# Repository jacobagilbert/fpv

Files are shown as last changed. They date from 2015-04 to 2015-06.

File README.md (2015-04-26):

# Custom FPV Related Software and Hardware
This repository contains various FPV related projects. These are side projects for me, and are free for anyone to use under the MIT license. I welcome anyone who would like to help improve on these!

I will attempt to keep this readme up-to-date and provide all resources I have used.

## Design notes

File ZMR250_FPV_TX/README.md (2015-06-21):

# Custom FPV Transmitter for ZMR250: The ZTX-23

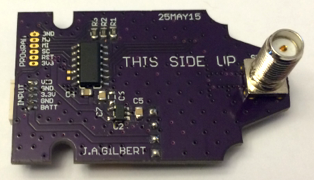
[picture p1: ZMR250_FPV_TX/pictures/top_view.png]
ZMR250 Top View


I suggest you read this entire README prior to building this, it's not that long and there are a few important considerations.

### Version 1.2 Changelog:

The version 1.2 hardware has resolved a few issues and annoyances:

- Addition of LDO to resolve SMPS noise in video
- Input connector is now a 5-pin picoblade to distinguish from the programming header
- Changed footprint for 7343 capacitors
- Switch and LED positions are changed for easier access
- Requires modification of the Pololu module

The remainder of this guide is for v1.2 only.

### Origins:

I had a number of annoyances related to the BOSCAM FPV transmitter I initially purchased for my ZRM250 quadcopter. It was difficult to change frequencies, mounting wasn't ideal, and most of all for whatever reason, it only put out 13.1 dBm (~20mW). I knew I was going to need another one, and I happened to stumble across a [German RC forum post](http://fpv-treff.de/viewtopic.php?f=23&t=5974) where an awesome guy developed a custom transmitter based around the TX5823 200mW 5.8GHz transmitter found in many pre-packaged FPV transmitters. While not exactly what I wanted, it was a great starting point and served as the inspiration for this project.

There are a number of differences from the original work, specifically the ATTiny software and PCB layout are completely new, but they get a ton of credit for all the great stuff in that forum .

### Project Objectives:

This project seeks to produce a 200mW FPV transmitter with the following specifications:

- Easily mounted securely on the ZMR250 frame
- Low profile and does not inhibit use of 6" propellers
- Simple to change channels (no buried DIP switches!)
- Direct 3S/4S power input
- Has frequency agility supporting all current receiver channels (including IRC's new 'RaceBand'!)

### Current System Status Overview:

**ATTiny Firmware:** The current ATTiny firmware has been tested on the hardware platform successfully! There are no known issues with the current software. I have used it many times and overall I am quite pleased. All 5 bands (40 channels total) have been implemented.

**Hardware:** The v2.1 boards are in and have been populated and tested - they function great. These were made through OSHPark and can be ordered [here](https://oshpark.com/shared_projects/h9UIDucG) - $12 for 3 copies. There are several optional components, which are detailed in a subsequent section.

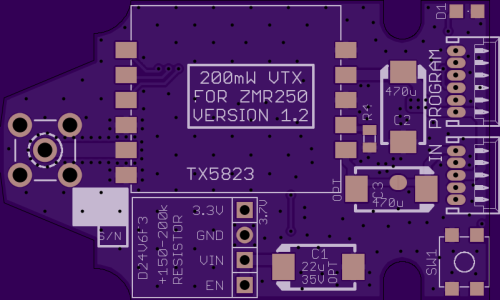
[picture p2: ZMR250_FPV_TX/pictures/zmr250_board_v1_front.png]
ZMR250 PCB Front


The RF path is a properly dimensioned CPWG transmission line, and while just at the length where it begins to matter (and it's FR4 at 5.8 GHz...), I figured it would be fun to do it properly. The trace is 55 mils wide with 9 mil spacing on 1.6 mm FR4, so the line has an impedance of between 49 and 51 ohms depending on the dielectric constant (I assume it's somewhere between 4.3 and 4.6 which should be reasonable).

**Weight:** While reducing weight was not a project objective, 250 racers and their pilots are weight-conscious if not sensitive. I made a few measurements and here is how this transmitter measures up. I was previously using a TS351 in a neat 3D printed holder, but it was pretty heavy:

| Hardware | Weight | Comments |
|---|---|---|
|BOSCAM TS351  |23.7g |Transmitter only, no mounting hardware |
|TS5823 |8g |Transmitter only, no mounting hardware |
|ZTX-23 |**13.3g** |Includes all mounting and cables! |
|SMA Extension |7g |30.7g with BOSCAM and no mounting hardware |

So this transmitter is not the lightest transmitter out there, but considering this includes all material required to securely install the transmitter to the frame, I am very pleased.

**Video Quality:** The ZTX-23 works really great. I tested bypassing the 3.3V LDO and using the Pololu module output directly, and one module looked okay, while the other had significant noise. With the LDO, crystal clear video. At this point I recommend using the LDO (it's ~$0.50) and making the modification to the Pololu module mentioned below.

### Repository Structure:

- eagle/			Eagle PCB files
- attiny/			ATTiny related files and firmware for board
- FPV_TX_BOM.xlsx		Bill of materials to populate boards
- ZMR250_FPV_TX_v1.2.zip	Compressed archive of all gerber files
- README_v1.0.md		Version 1.0 README, out of date but preserved
- README.md			This README

### Bill of Materials:

BOM is up. There are only a handful of components, but the large capacitors are all 7343 size tantalum and the small capacitors are all 0.1uf decoupling caps, the Pololu module is a 500mA 3.3V SMPS, R1 is 330 ohm and R2/R3 are 3.3k. The LDO (U2) is an AP2112 3.3V fixed-output reg. All the small passives are 0805 (however SparkFun's 0805 footprint is a little tight... If you have them, use 0603 for bypass capacitor and resistors).

### Component Modifications:

Both the TX5823 module and Pololu SMPS must be modified before they can be used for this application.

**TX5823 Module Modifications:** It is necessary to modify the TX5823 module so it is able to operate in SPI mode. The modification only require the removal of a single resistor, however it is under the metal shield on the module so you will need to remove that first. This information is available in either the datasheet of the RTC6705 chip.

The easiest way to make the modification is to work one side at a time (they are soldered on two sides) with a soldering iron and precision slotted screwdriver. Use the screwdriver between the module board and shield to *gently* apply pressure while melting the solder. If you work carefully, alternating sides, and taking breaks to allow the module to cool down it is fairly easy to remove the shield. Clean up any excess solder, and remove the resistor shown in the following image:

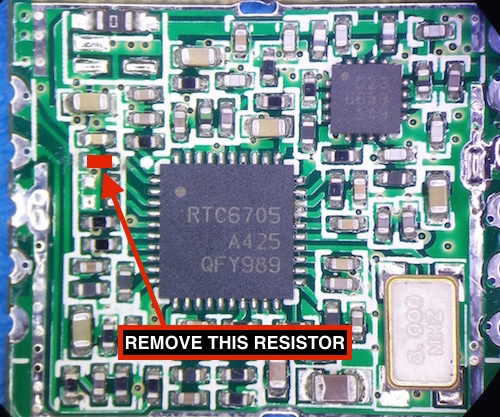
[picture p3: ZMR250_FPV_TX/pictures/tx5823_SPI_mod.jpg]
TX5823 Module RX5823 with shield removed


After removing the resistor, inspect the board (preferrably under a magnifying glass) to ensure you have not accidentally caused any shorts or displaced any other components; replace the shield. This only needs to be done once so you can re-solder the shield to the module PCB.

More information regarding SPI mode operation is available in the limited datasheet, and under the 'attiny' directory.

**Pololu Module Modification:** In order to use the 3.3V LDO, the input must be around 3.6V due to the dropout voltage. This requires a change in the Pololu module, which fortunately is simple - soldering a resistor in parallel with 22.1k R2 on the Pololu module will increase the module output voltage by approximately 350mV and will properly power the LDO. This combination has good efficency on 3S/4S and provides clean power.

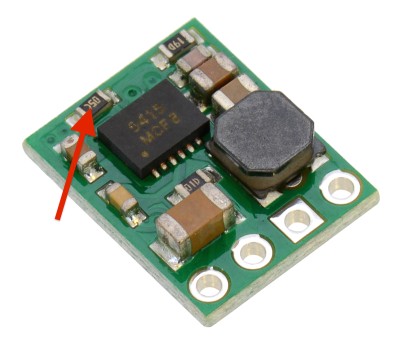
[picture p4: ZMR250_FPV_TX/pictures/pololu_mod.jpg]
Pololu SMPS Pololu Resistor Change


The resistor that must be changed by adding another in parallel is shown above, simply solder a ~150k resistor in parallel with it. This value can be deterined from the datasheet for the SMPS controller used, available from Pololu.

### Mounting Transmitter:

One of the design criteria for this transmitter was mounting natively to the ZMR250 frame. Consistant with that, it has been designed to mount cleanly to the rear of the top plate, though the hole in the rear must be drilled out with a 0.25" bit to accomodate the SMA connector. By mounting the SMA connector directly to the frame, it is very unlikely that a crash will damage the transmitter. Be careful drilling carbon fiber as it can be a little tricky, and don't inhale the dust!

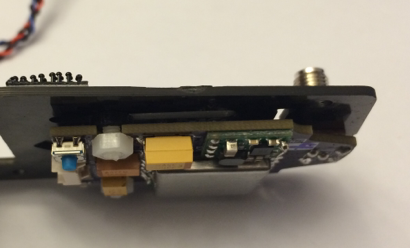
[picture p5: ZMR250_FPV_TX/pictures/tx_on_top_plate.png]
TX Mounted Transmitter on top plate


On the other end from the SMA connector are two slots that will nicely fit M3 nylon hardware. A spacer is needed to keep some standoff from the conductive frame. I used the smallest diameter HQ propeller mounting bushings since they were a pretty good fit but I'll probably 3D print some spacers that are sized better and post the files when I am happy.

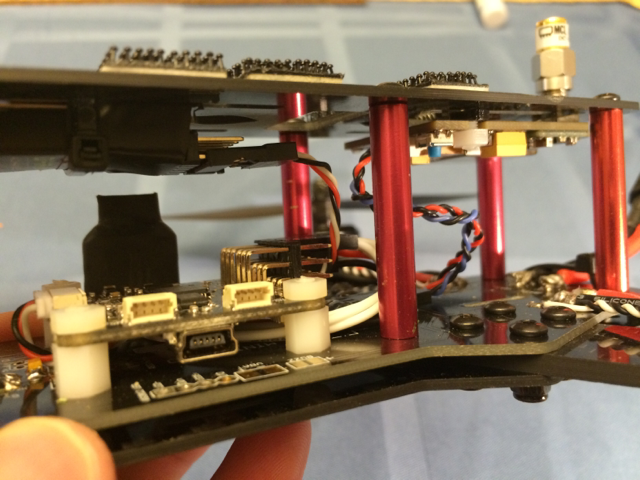
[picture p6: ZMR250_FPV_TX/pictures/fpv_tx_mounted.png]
Mounting Mounting FPV Transmitter


### Connectors:

There are two connectors on the board, a 5 pin Molex PicoBlade PTH connector for power and video input, and a 6 pin PicoBlade PTH connector for programming. I recommend populating only the 5 pin input connector so they are not confused when conecting hardware. To program the microcontroller, I bend the pins slightly on the 6 pin header so they press-fit securely and remove the connector when I am through.

### Transmitter Operation:

The transmitter will remember the last channel used and will automatically configure to this channel on startup. To view the current frequency, you can push the button once quickly and the LED will flash the current band (1-5) followed by a brief pause, followed by the current channel (1-8). To change the frequency, the following procedure should be used:

1. Press and hold the button until the LED turns off and immediately release it. In order to prevent accidental channel changing if you hold it too long, or release it too early it will not set the frequency.
2. The LED will flash quickly and stop. Press the button to set the band (eg: 3 presses will select band 3, "Band E"). If you press the button more than 5 times (the total number of supported bands), it will loop back to 1.
3. Wait for the LED to flash quickly again and set the channel using the same procedure as above. There are 8 channels in each band, and pressing more than 8 times will loop back to 1.
4. Release the button and wait for confirmation that the band has been set (flashes indicating the band, followed by the channel). The transmitter is now reconfigured and will immediately update the frequency of the module, and will start with the new channel in the future.
5. If the button is not pressed to select the band or channel, the frequency selection mode will exit and flash the LED quickly many times. There will be no change to the current or startup channel.

I think I like this scheme but I'm not sure; it might change. Either way, it's a good start that only requires one button and one LED.

### Optional Components:

**Video Input Capacitor:** The TX5823 module specifies a 470uF capacitor on the video input line (C3). These are rather expensive, and I'm not sure it is strictly necessary so I added pads that can be solder-jumpered to bypass the capacitor. I have tested both with and without this cap, and could not see a difference. I will most likely not purchase these again.

**Pololu Module Capacitor:** Pololu recommends the use of a large value capacitor to prevent damage from any turn-on voltage spike. They suggest an input of under 20V with short leads should be fine, but I included the pads anyway. I include them just in case, but like the video input cap, these are fairly expensive. If you do use one, make sure it is rated for the appropriate voltage.

**Audio Grounding Resistor:** I included pads for a resistor (R4) that can be used to terminate the audio input, which is no longer connected to the input connector. Feel free to omit this.

**Noise Reduction Capacitor:** The LDO NR capacitor (C6) should only be used with LDOs that require this. The AP2112 I have in the BOM has this pin as a NC and thus C6 should NOT be populated.

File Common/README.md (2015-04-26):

# Common files and components

Here are common components such as libraries for Eagle or Arduino, as well as datasheets for parts and other useful but not project-specific items.

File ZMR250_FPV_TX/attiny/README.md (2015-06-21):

# ATTiny Related Documents

The ATTiny84 firmware was written in Arduino because it's quick and easy, and I want the project to be approachable by non-professionals. I'll try to upload a hex file at some point though for those who are not Arduino inclined. Programming instructions are based on the [work by HighLowTech](http://highlowtech.org/?p=1695) and are pretty straightforward. A dedicated programming header is located on the board, but that might be removed in future versions since firmware should not need to change very often.

I targeted an ATTiny84 because it fit and they are still relatively inexpensive, and it let me be lazy in programming and layout, and it does not require dual-purposing pins. The sketch will compile for an ATTiny44, and shouldn't be too hard to get into an ATTiny24. Currently the Arduino IDE reports the program size as 2,156 bytes (26% of the ATTiny84).

### Files:

- attiny84_transmitter.ino	Arduino 1.6 sketch for ATTiny84
- attiny_arduino_1.6.zip	ATTiny support for Arduino 1.6
- TX_Channel_Calculator.xlsx	Excel spreadsheet for calculating register values

### Programming the ATTiny

It is important to note that the ATTiny runs from the same 3.3V supply as the video transmitter, and the VTX will be powered anytime the ATTiny is! Be sure to connect an antenna, or terminate the SMA connector so the RFIC output stage is not damaged by reflected power. The board has a dedicated programming port and current-limiting resistors on MOSI and SCK lines to allow for programming from a 5V arduino device. I don't have a dedicated Atmel programmer, so this is what I do.

This is what I do to program: connect RST, MOSI, MISO, SCK, and GND from connector X3 to pins 10-13 + GND on an Arduino board with the Arduino ISP sketch loaded. Terminate the antenna port and then apply power to VBATT on connector X2. Then hit the upload button on the Arduino IDE. The first time you program the chip, before you program, you need to make sure "internal 8MHz" is selected for clock source and burn the bootloader. The link above covers this in much better detail.

### Register Settings

The RTC6705 RFIC has two 20-bit registers that control the frequency synthesizer, 0x00 and 0x01. The 0x00 (Synthesizer Register A) register contains the R-counter divider in the low 15 bits. The 0x01 register contains the N-counter divider in the upper 13 bits and the A-counter divider in the lower 7 bits.

The default R-counter divider value (0x190 = 400d) provides for 40kHz tuning resolution, which is more than sufficient, so it is not changed. The values for the 0x01 register for each channel are pre-calculated and stored in PROGMEM. These values were derived from the equations in the TX_Channel_Calculator spreadsheet.

At initial turn-on, the registers are set to the last stored frequency which is written to onboard EEPROM after every successful channel change. This initial frequency setting procedure is performed several times at startup after varying delay. This is to reduce the amount of interference the default settings might cause to other FPV fliers in the area. 100ms delay proved too short to reliably tune the TX chip, so we attempt to tune it to the last known frequency after 100ms, 300ms, and 500ms - if it's stupid and it works it's not stupid :).

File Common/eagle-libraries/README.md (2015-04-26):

# Common Libraries
This directory contains libraries used by the various projects, both those developed by me, and archived versions of commercial/other libraries that I have incorporated.

## BOSCAM_5G8.lbr
Eagle library contianing BOSCAM 5.8GHz modules:

1. TX5823 200mW FM Transmitter (pin compatible with 10mW TX5813)

2. RX5808 FM Receiver (identical to RX5880)

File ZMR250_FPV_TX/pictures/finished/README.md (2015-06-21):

### IMAGE PREVIEW:

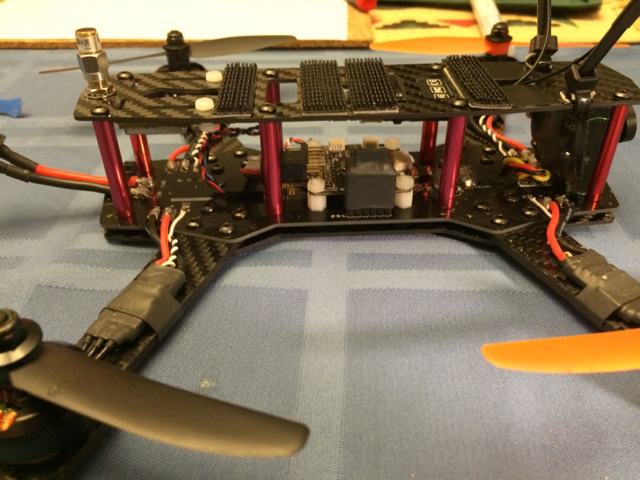
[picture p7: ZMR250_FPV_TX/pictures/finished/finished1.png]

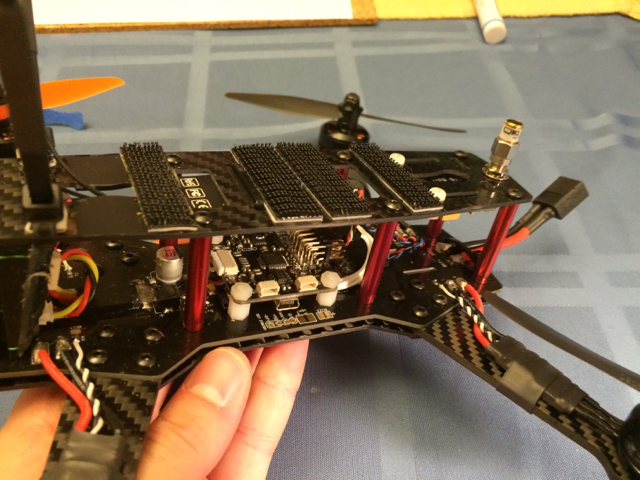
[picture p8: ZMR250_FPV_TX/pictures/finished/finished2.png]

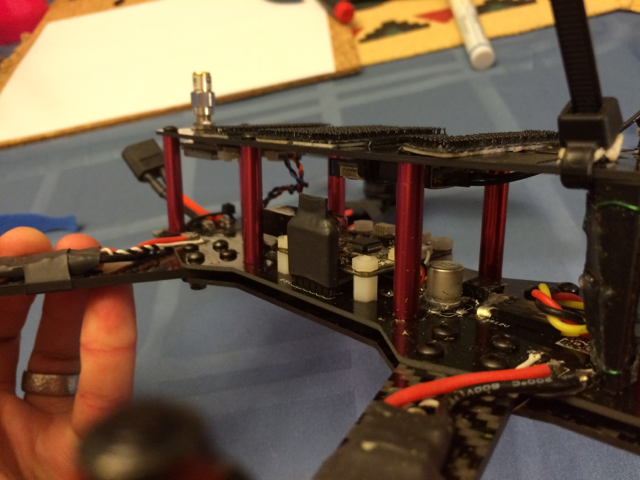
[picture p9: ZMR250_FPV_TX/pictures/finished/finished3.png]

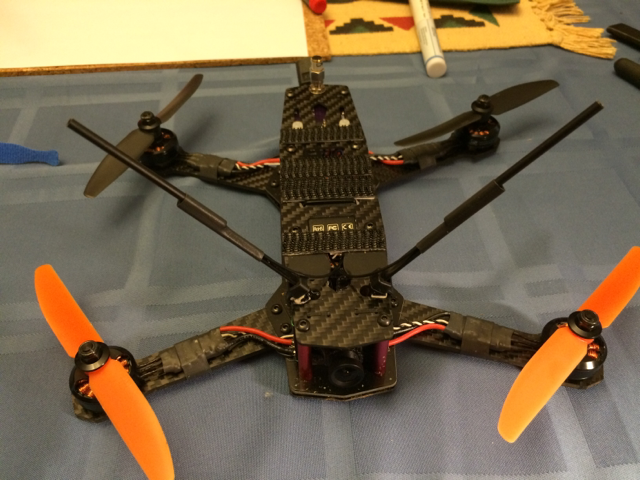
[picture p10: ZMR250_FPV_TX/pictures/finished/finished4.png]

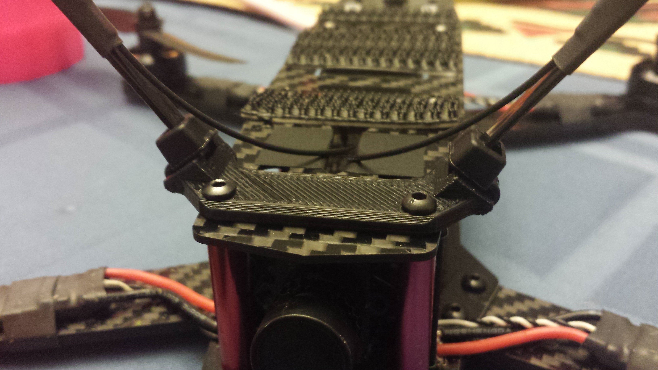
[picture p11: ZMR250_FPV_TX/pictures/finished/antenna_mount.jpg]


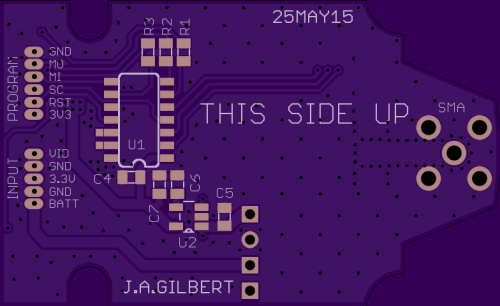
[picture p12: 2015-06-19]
ZMR250_FPV_TX/pictures/zmr250_board_v1_back.png

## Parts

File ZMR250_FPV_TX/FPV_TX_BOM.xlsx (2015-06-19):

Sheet: BOM-TXv1.0
 |  |  |  | Quantity
Name | Specs | Digikey Part Number | Digikey Link | Per board | Suggested
Connector | 6 pin male | WM1746-ND | http://www.digikey.com/product-detail/en/0530480610/WM1746-ND/242868 | 2 | 2
Connector | 6 Pin female | WM1724-ND | http://www.digikey.com/product-detail/en/0510210600/WM1724-ND/242846 | 2 | 2
Connector | Female Pins | WM1142CT-ND | http://www.digikey.com/product-detail/en/0500798000/WM1142CT-ND/467835 | 12 | 25
SMA | Tall | CONSMA008-ND | http://www.digikey.com/product-detail/en/CONSMA008/CONSMA008-ND/1577219 | 1 | 1
uC | ATTiny | ATTINY84A-SSU-ND | http://www.digikey.com/product-detail/en/ATTINY84A-SSU/ATTINY84A-SSU-ND/3046522 | 1 | 1
Resistor | 0805 / 3.3k | RHM3.30KCHCT-ND | http://www.digikey.com/product-detail/en/MCR10ERTF3301/RHM3.30KCHCT-ND/2796529 | 3 | 10
Resistor | 0805 / 1k | RHM1.00KCHCT-ND | http://www.digikey.com/product-detail/en/MCR10ERTF1001/RHM1.00KCHCT-ND/2796512 | 3 | 10
Resistor | 0805 / 330 | RHM330CHCT-ND | http://www.digikey.com/product-detail/en/MCR10ERTF3300/RHM330CHCT-ND/2796528 | 1 | 1
LED | Green (2.1V) | 160-1423-1-ND | http://www.digikey.com/product-detail/en/LTST-C171GKT/160-1423-1-ND/386792 | 1 | 1
Module Cap | 470uF | 478-4146-1-ND | http://www.digikey.com/product-detail/en/TPSE477K006R0050/478-4146-1-ND/1164482 | 1 | 1
Switch | SPST | 7914G-000ECT-ND | http://www.digikey.com/product-detail/en/7914G-1-000E/7914G-000ECT-ND/158366 | 1 | 1
Capacitor | Decoupling | 399-1284-1-ND | http://www.digikey.com/product-detail/en/C0805C105K4RACTU/399-1284-1-ND/416060 | 1 | 10
Pololu Cap | 35V/33u | 399-8536-1-ND | http://www.digikey.com/product-detail/en/T495X336K035ATE250/399-8536-1-ND/3472259 | 1 | 1
Video Cap | Video | 478-9450-1-ND | http://www.digikey.com/product-detail/en/TCJD477M002R0050/478-9450-1-ND/5001662 | 1 | 1
Not Digikey Stuff
Plolou SMPS | 3.3V / 500mA | D24V5F3 | https://www.pololu.com/product/2842 | 1 | 1
TX Module |  |  | http://www.foxtechfpv.com/tx5823-200mw-8ch-58g-tx-module-for-nano-flyers-p-272.html | 1 | 1
Boards |  |  | OSHPark | 1 | 1

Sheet: BOM-TXv1.2
 |  |  |  | Quantity
Name | Specs | Digikey Part Number | Digikey Link | Per board | Suggested | Comments
Connector | 5 pin male | WM1745-ND | http://www.digikey.com/product-detail/en/0530480510/WM1745-ND/242867 | 1 | 1
Connector | 5 Pin female | WM1723-ND | http://www.digikey.com/product-detail/en/0510210500/WM1723-ND/242845 | 1 | 1
Connector | 6 pin male | WM1746-ND | http://www.digikey.com/product-detail/en/0530480610/WM1746-ND/242868 | 1 | 1
Connector | 6 Pin female | WM1724-ND | http://www.digikey.com/product-detail/en/0510210600/WM1724-ND/242846 | 1 | 1
Connector | Female Pins | WM1142CT-ND | http://www.digikey.com/product-detail/en/0500798000/WM1142CT-ND/467835 | 11 | 25
SMA | Tall | CONSMA008-ND | http://www.digikey.com/product-detail/en/CONSMA008/CONSMA008-ND/1577219 | 1 | 1
uC | ATTiny | ATTINY84A-SSU-ND | http://www.digikey.com/product-detail/en/ATTINY84A-SSU/ATTINY84A-SSU-ND/3046522 | 1 | 1
LDO | 3.3V / 600mA | AP2112K-3.3TRG1DICT-ND | http://www.digikey.com/product-detail/en/AP2112K-3.3TRG1/AP2112K-3.3TRG1DICT-ND/4505257 | 1 | 1
Resistor | 0805 / 150k | RHM150kCHCT-ND | http://www.digikey.com/product-detail/en/MCR10ERTF1503/RHM150KCHCT-ND/4084575 | 1 | 1 | For SMPS
Resistor | 0805 / 3.3k | RHM3.30KCHCT-ND | http://www.digikey.com/product-detail/en/MCR10ERTF3301/RHM3.30KCHCT-ND/2796529 | 4 | 10
Resistor | 0805 / 330 | RHM330CHCT-ND | http://www.digikey.com/product-detail/en/MCR10ERTF3300/RHM330CHCT-ND/2796528 | 1 | 1
LED | Green (2.1V) | 160-1423-1-ND | http://www.digikey.com/product-detail/en/LTST-C171GKT/160-1423-1-ND/386792 | 1 | 1
Switch | SPST | 7914G-000ECT-ND | http://www.digikey.com/product-detail/en/7914G-1-000E/7914G-000ECT-ND/158366 | 1 | 1
Module Cap | 470uF | 478-4146-1-ND | http://www.digikey.com/product-detail/en/TPSE477K006R0050/478-4146-1-ND/1164482 | 1 | 1
Capacitor | Decoupling | 399-1284-1-ND | http://www.digikey.com/product-detail/en/C0805C105K4RACTU/399-1284-1-ND/416060 | 4 | 10
Pololu Cap | 35V/33u | 399-8536-1-ND | http://www.digikey.com/product-detail/en/T495X336K035ATE250/399-8536-1-ND/3472259 | 1 | 1 | OPTIONAL?
Video Cap | Video | 478-9450-1-ND | http://www.digikey.com/product-detail/en/TCJD477M002R0050/478-9450-1-ND/5001662 | 1 | 1 | OPTIONAL?
Not Digikey Stuff
Plolou SMPS | 3.3V / 500mA | D24V5F3 | https://www.pololu.com/product/2842 | 1 | 1
TX Module | 200mW 5.8G | TX5823 | http://www.foxtechfpv.com/tx5823-200mw-8ch-58g-tx-module-for-nano-flyers-p-272.html | 1 | 1
PCB |  |  | OSHPark | 1 | 1
Wire | 28/30 AWG |  | Recommend 30AWG silicon wire - for connector cables

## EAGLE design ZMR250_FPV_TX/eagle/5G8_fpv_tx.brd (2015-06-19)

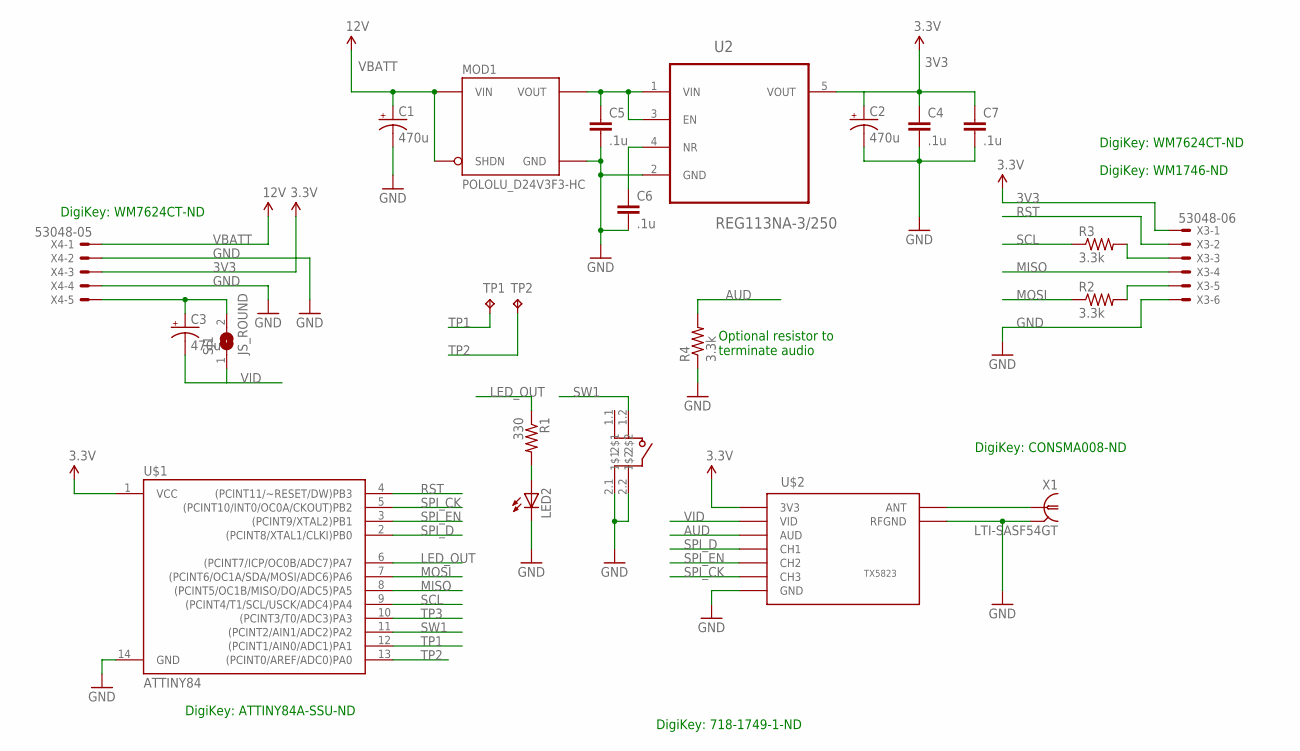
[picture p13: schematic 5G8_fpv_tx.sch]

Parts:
C1, C2, C3: 470u; VISHAY_D
C4, C5, C6, C7: .1u; 0805
LED2: LEDCHIPLED_0805; CHIPLED_0805
MOD1: POLOLU_D24V3F3-HC; POLOLU_D24V3F_HC
R1: 330; 0805
R2, R3, R4: 3.3k; 0805
SJ1: JS_ROUND; SJ_ROUND
TP1, TP2: TPTP06SQ; TP06SQ
U2: REG113NA-3/250; SOT95P280X145-5N
U$1: ATTINY84; SO14
U$2: TX5823
U$3: BOURNS_7814G_SW; 7914G
X1: LTI-SASF54GT
X3: 53048-06
X4: 53048-05

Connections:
3V3: C2.+, C4.1, C7.1, U2.5 (VOUT), U$1.1 (VCC), U$2.P$4 (3V3), X3.1, X4.3
ANT: U$2.P$10 (ANT), X1.1
AUD: R4.2, U$2.P$2 (AUD)
GND: C1.-, C2.-, C4.2, C5.2, C6.2, C7.2, LED2.C, MOD1.G (GND), R4.1, U2.2 (GND), U$1.14 (GND), U$2.P$3 (GND), U$2.P$5 (GND), U$2.P$9 (RFGND), U$2.P$11 (RFGND), U$3.2.1 (2$1), U$3.2.2 (2$2), X1.2, X1.3 (2), X1.4 (2), X1.5 (2), X3.6, X4.2, X4.4
LED: LED2.A, R1.2
LED_OUT: R1.1, U$1.6 ((PCINT7/ICP/OC0B/ADC7)PA7)
MISO: U$1.8 ((PCINT5/OC1B/MISO/DO/ADC5)PA5), X3.4
MOSI: R2.1, U$1.7 ((PCINT6/OC1A/SDA/MOSI/ADC6)PA6)
MOSI_: R2.2, X3.5
unnamed: C5.1, MOD1.O (VOUT), U2.1 (VIN), U2.3 (EN)
unnamed: C6.1, U2.4 (NR)
RST: U$1.4 ((PCINT11/~RESET/DW)PB3), X3.2
SCL: R3.1, U$1.9 ((PCINT4/T1/SCL/USCK/ADC4)PA4)
SCL_: R3.2, X3.3
SPI_CK: U$1.5 ((PCINT10/INT0/OC0A/CKOUT)PB2), U$2.P$8 (CH3)
SPI_D: U$1.2 ((PCINT8/XTAL1/CLKI)PB0), U$2.P$6 (CH1)
SPI_EN: U$1.3 ((PCINT9/XTAL2)PB1), U$2.P$7 (CH2)
SW1: U$1.11 ((PCINT2/AIN1/ADC2)PA2), U$3.1.2 (1$2)
TP1: TP1.TP, U$1.12 ((PCINT1/AIN0/ADC1)PA1)
TP2: TP2.TP, U$1.13 ((PCINT0/AREF/ADC0)PA0)
TP3: U$1.10 ((PCINT3/T0/ADC3)PA3)
VBATT: C1.+, MOD1.I (VIN), MOD1.S (SHDN), X4.1
VID: C3.-, SJ1.1, U$2.P$1 (VID)
VID_IN: C3.+, SJ1.2, X4.5

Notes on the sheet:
DigiKey: WM7624CT-ND
DigiKey: ATTINY84A-SSU-ND
DigiKey: CONSMA008-ND
DigiKey: 718-1749-1-ND
DigiKey: WM1746-ND
Optional resistor to terminate audio

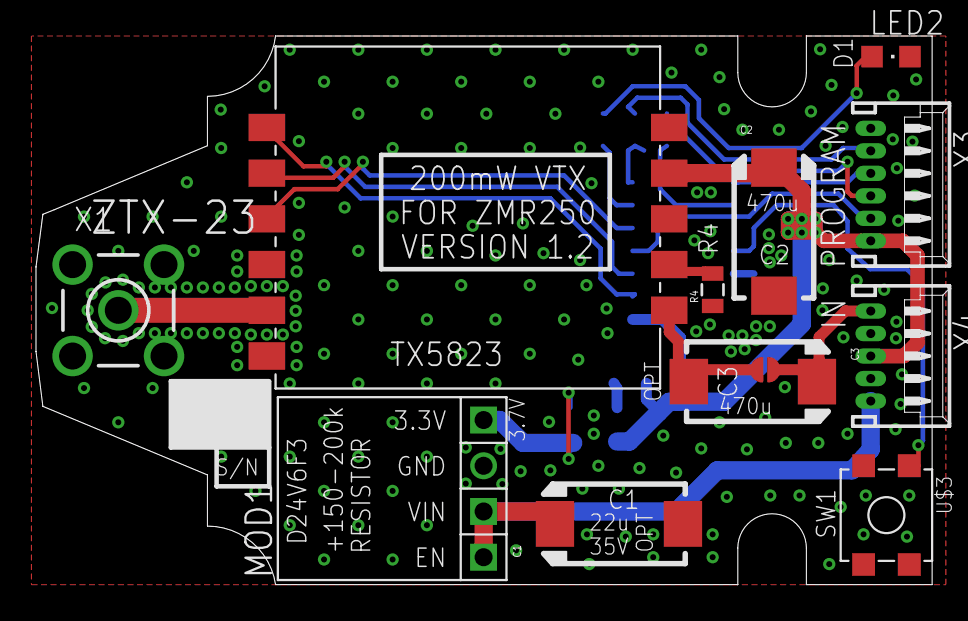
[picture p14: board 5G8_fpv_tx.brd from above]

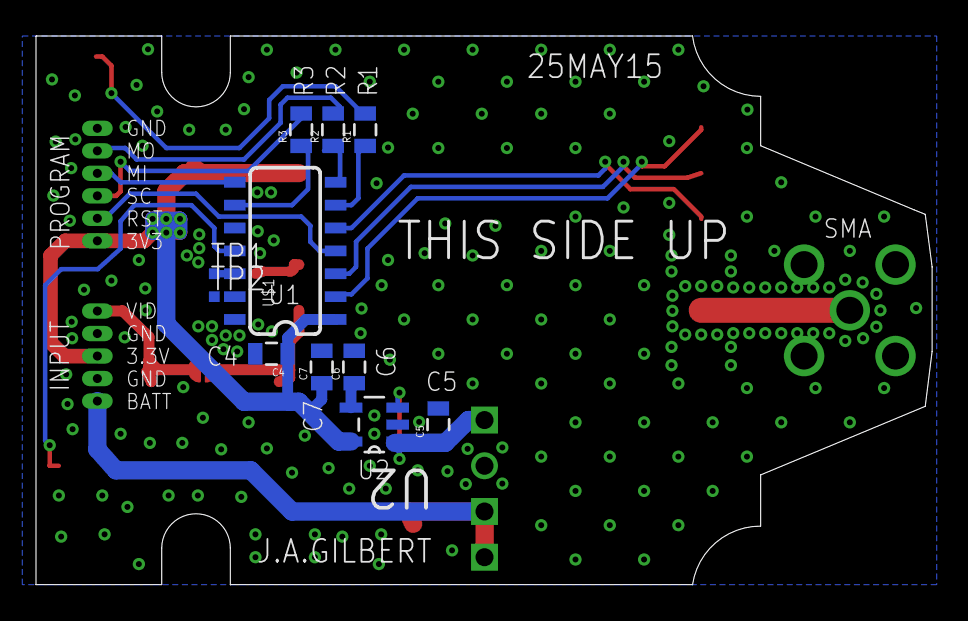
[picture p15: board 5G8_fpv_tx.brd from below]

Board: 2 copper layers, 49.8 x 30.5 mm, 23 parts (11 on the bottom side), 23 nets.

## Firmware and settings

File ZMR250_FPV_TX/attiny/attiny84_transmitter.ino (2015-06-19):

/*
 *  BOSCAM TX5823-based 5.8Ghz 200mW FPV transmitter
 *
 *  Author: J. A. Gilbert
 *  Date:   April 2015
 *  Info:   https://github.com/mrjacobagilbert/fpv
 *  
 *  Description:
 *    This code is designed for the ATTiny44/84, with optimization it may run on a 24. It
 *    will display the current band/channel on startup, set the frequency and wait for
 *    user input. The operator can change frequency with a long button press and a quick
 *    release after the LED turns on.
 *
 *
 *  Programming Information:
 *    Using ArduinoISP sketch, connect the following pins. 3.3k resistors should be used
 *    if the output is higher voltage than the input (eg: on RST/SCK/MOSI if Arduino is +5V
 *    and ATTiny is +3.3v, MISO does not need one).
 *
 *       ARDUINO              ATTINY
 *         D10 ----------->> RST  (4)
 *         D11 ----------->> MOSI (7)
 *         D12 <<----------- MISO (8)
 *         D13 ----------->> SCK  (9)
 *         GND ------------- GND (14)
 *
 *  This sketch is designed to run with an 8MHz oscillator. Burn the appropriate bootloader.
 */
 
#include <EEPROM.h>

static const uint8_t SPI_ENABLE_PIN = 9;        // ATTiny Pin 3
static const uint8_t SPI_CLOCK_PIN = 8;         // ATTiny Pin 5
static const uint8_t SPI_DATA_PIN = 10;         // ATTiny Pin 2
static const uint8_t SWITCH_PIN = 2;            // ATTiny Pin 11
static const uint8_t LED_PIN = 7;               // ATTiny Pin 6
static const uint8_t REMOTE_PIN = 0;            // ATTiny Pin 13

static const uint8_t EEPROM_ADDR_LAST_FREQ = 1;
static const uint8_t NUM_BANDS = 5;

/* These frequencies are for RichWave transmitters - this table is the lower 16 bits - upper 4 bits are 0x4 */
static const uint16_t channelTable[] PROGMEM = {
//   CH 1       CH 2       CH 3       CH 4       CH 5       CH 6       CH 7       CH 8
    0x7981,    0x758D,    0x7199,    0x6DA5,    0x69B1,    0x65BD,    0x6209,    0x5E15,    // Band A
    0x5F9D,    0x6338,    0x6713,    0x6AAE,    0x6E89,    0x7224,    0x75BF,    0x799A,    // Band B
    0x5A21,    0x562D,    0x5239,    0x4E85,    0x7D35,    0x8129,    0x851D,    0x8911,    // Band E
    0x610C,    0x6500,    0x68B4,    0x6CA8,    0x709C,    0x7490,    0x7884,    0x7C38,    // Band F / Airwave
    0x510A,    0x5827,    0x5F84,    0x66A1,    0x6DBE,    0x751B,    0x7C38,    0x8395     // Band R / Raceband
};
static const uint16_t rCounter = 0x0190;    // default value, provides 40kHz frequency resolution

/* Frequency mapping for channelTable (values in MHz):
 *   CH 1       CH 2       CH 3       CH 4       CH 5       CH 6       CH 7       CH 8
 *   5865       5845       5825       5805       5785       5765       5745       5725      // Band A
 *   5733       5752       5771       5790       5809       5828       5847       5866      // Band B
 *   5705       5685       5665       5645       5885       5905       5925       5945      // Band E
 *   5740       5760       5780       5800       5820       5840       5860       5880      // Band F / Airwave
 *   5658       5695       5732       5769       5806       5843       5880       5917      // Band R / RaceBand
 */

enum STATE { WAITING, HOLDOFF, SHOW_FREQ, RELEASE_TIMER, BAND_COUNTING, CHANNEL_COUNTING, SET_FREQ } current_state;
uint16_t count;
uint8_t current_freq, previous_val, band, channel;
uint8_t n_ctr = 0;

void setup() {
  
  // set pin directions
  pinMode(SPI_ENABLE_PIN, OUTPUT);
  pinMode(SPI_CLOCK_PIN, OUTPUT);
  pinMode(SPI_DATA_PIN, OUTPUT);
  pinMode(SWITCH_PIN, INPUT_PULLUP);
  pinMode(LED_PIN, OUTPUT);
  pinMode(REMOTE_PIN, INPUT_PULLUP);
  
  // initialize SPI bus
  digitalWrite(SPI_CLOCK_PIN, LOW);
  digitalWrite(SPI_ENABLE_PIN, HIGH);
  
  // LED is OFF by default
  digitalWrite(LED_PIN, LOW);

  // read previous channel from EEPROM
  current_freq = EEPROM.read(EEPROM_ADDR_LAST_FREQ) & 0x3f;  // mask by 0b0011.1111 = 0b xx xx B2 B1 . B0 C2 C1 C0

  // give transmitter time to power up before setting frequency
  delay(100);

  // set the frequency on the module
  set_5823_freq(current_freq);
  
  // now do that 3 more times to make sure it took - we could wait longer but want to minimize
  // any interference we might be caused by us powering up to the default frequency
  delay(100);
  set_5823_freq(current_freq);
  delay(100);
  set_5823_freq(current_freq);
  
  //flash current frequency to user on boot
  flashFreq(current_freq);
  
  current_state = WAITING;
}

void loop() {
  
  // main loop is just a switch statement
  switch (current_state) {
    
//----------------------- WAITING FOR USER INPUT ----------------------------//
    case WAITING:
      if (button_read(10)) {
        current_state = HOLDOFF;
        count = 0;
      } else {
        // LED heartbeat
        if ((n_ctr > 0xc0) && ((n_ctr & 0x1f) > 0x18)) {
          digitalWrite(LED_PIN, HIGH);
        } else {
          digitalWrite(LED_PIN, LOW);
        }
        n_ctr++;
      }
      break;
      
//----------------------- CHECKING DURATION OF BUTTON PRESS -----------------//
    // must hold button for two seconds
    case HOLDOFF:
      if (count > 200) {
        digitalWrite(LED_PIN, HIGH);
        count = 0;
        current_state = RELEASE_TIMER;
      } else {
        if (!button_read(10)) {
          // if just a quick press, flash the frequency
          if (count < 25) {
            current_state = SHOW_FREQ;
            digitalWrite(LED_PIN, LOW);
          } else {
            current_state = WAITING;
            digitalWrite(LED_PIN, LOW);
          }
        }
      }
      count++;
      break;
      
//----------------------- DISPLAY FREQUENCY FOR SHORT PRESS -----------------//
    case SHOW_FREQ:
      flashFreq(current_freq);
      current_state = WAITING;
      break;
      
//----------------------- CHECKING FOR BUTTON RELEASE -----------------------//
    // must release button within 350 ms of LED going off
    case RELEASE_TIMER:
      if (!button_read(10)) {
        if (count > 35) {
          digitalWrite(LED_PIN, LOW);
          current_state = WAITING;
        } else {
          digitalWrite(LED_PIN, LOW);
          
          // indicate band-setting mode when released
          delay(500);
          blink_led(25,75,5);
          count = 0;
          band = 0;
          previous_val = 0;
          current_state = BAND_COUNTING;
        }
      } else {
        if (count > 30) {
          digitalWrite(LED_PIN, LOW);
        }
      }
      count++;
      break;
      
//----------------------- USER BAND SELECTION -------------------------------//
    case BAND_COUNTING:
      if (button_read(10)) {
        if (previous_val == 0) {
          blink_led(20,0,1);
          count = 0;    // reset the counter if button was pressed
          band++;
          // not all bands are valid, loop back around if too many presses
          if (band > NUM_BANDS) {  
            band -= NUM_BANDS;
            delay(100);
            blink_led(20,0,1);
          }
        }
        previous_val = 1;
      } else {
        previous_val = 0;
        count++;
      }
      // after 2 seconds of no button presses, continue
      if (count >= 200) {
        // if band is still zero, flash error sequence and go back to start
        if (band > 0) {
          // indicate band-setting mode when released
          delay(500);
          blink_led(75,25,5);
          count = 0;
          channel = 0;
          previous_val = 0;
          current_state = CHANNEL_COUNTING;
        } else {
          flashError();  // flash error sequence
          current_state = WAITING;
        }
      }
      break;
      
//----------------------- USER CHANNEL SELECTION ----------------------------//
    case CHANNEL_COUNTING:
      if (button_read(10)) {
        if (previous_val == 0) {
          blink_led(20,0,1);
          count = 0;    // reset the counter if button was pressed
          channel++;
          // only 8 possible channels, reset if too many presses
          if (channel > 8) {
            channel -= 8;
            delay(100);
            blink_led(20,0,1);
          }
        }
        previous_val = 1;
      } else {
        previous_val = 0;
        count++;
      }
      // after 2 seconds of no button presses, continue
      if (count >= 200) {
        // if band is still zero, flash error sequence and go back to start
        if (channel > 0) {
          delay(500);
          current_state = SET_FREQ;
        } else {
          flashError();     // flash error sequence
          current_state = WAITING;
        }
      }
      break;
      
//----------------------- SETTING FREQUENCY ---------------------------------//
    case SET_FREQ:
      current_freq = (band - 1) * 8 + (channel - 1);
      
      // save current freq to EEPROM
      EEPROM.write(EEPROM_ADDR_LAST_FREQ, current_freq);
      
      // set the current frequency of the module
      set_5823_freq(current_freq);
      
      // display the frequency to the user
      flashFreq(current_freq);
      
      current_state = WAITING;
      break;
      
//----------------------- BY DEFAULT, RETURN TO WAITING ---------------------//
    default:
      current_state = WAITING;
      break;
  }
}


/////////////////////////////////////////////////////////////////////////////////////////
//////////////////////////////////     SUBROUTINES     //////////////////////////////////
/////////////////////////////////////////////////////////////////////////////////////////

/*
 *  read the button applying a very simple software-debounce routine accepts
 *  configurable debounce time, favor unpressed ('1' due to internal pullup)
 */
byte button_read(uint16_t time)
{
  if (digitalRead(SWITCH_PIN) == 0) {
    delay(time);
    if (digitalRead(SWITCH_PIN) == 0) {
      return 1;
    }
  } else {
    delay(time);
  }
  return 0;
}


/*
 *  blink the LED with definable duty cycle and number of times
 */
void blink_led(uint16_t ms_on, uint16_t ms_off, uint16_t n_times)
{
  uint16_t ii;
  
  for (ii = n_times; ii > 0; ii--) {
    digitalWrite(LED_PIN, HIGH);
    delay(ms_on);
    digitalWrite(LED_PIN, LOW);
    delay(ms_off);
  }  
}


/*
 *  show the current frequency by blinking the LED
 */
void flashFreq(uint8_t freq)
{
  //blink_led(750,0,1);                        // long blink
  delay(750);                                // delay
  blink_led(100,200,((freq >> 3) + 1));      // band is bits 3-5
  delay(1000);                               // delay
  blink_led(100,200,((freq & 0x07) + 1));    // channel is bits 0-2
  delay(750);                                // delay
  //blink_led(750,0,1);                        // long blink
}


/*
 * display predefined LED error sequence - 16 fast blinks
 */
void flashError(void)
{
  blink_led(20, 30, 16);  // LED error sequence
}


/*
 *  update the frequency registers on TX5823
 */
void set_5823_freq(uint8_t freq)
{
  uint8_t i;
  uint32_t channelData;
  
  // if the band value is illegal, flash error sequence only
  if (freq >= (NUM_BANDS*8)) {
    flashError();  // flash LED error sequence
  } else {
    // read in the channel information from the table, and add 0x00 04 00 00 to it
    channelData = (pgm_read_word_near(channelTable + freq)) + 0x00040000;
    
    // Setting the R-Counter is not necessary every time but doesn't hurt
    spi_write(0x00, rCounter);      // write R counter-divider (fixed value)
    spi_write(0x01, channelData);   // write N and A counter-dividers (from channel table)
  }
}


/*
 * execute a complete SPI write operation
 */
void spi_write(uint8_t addr, uint32_t data)
{
  uint8_t i;
  uint32_t output;
  
  //              FIRST  -  -  -  -  -  -  -  -  -  -  -  LAST
  // Data Format: A0  A1  A2  A3  R/W  D0  D1  D2 ... D18  D19
  output = ((data << 5) | 0x10) + (addr & 0x0f);
  
  // start SPI transaction
  digitalWrite(SPI_CLOCK_PIN, LOW);
  digitalWrite(SPI_ENABLE_PIN, LOW);

  // clock out data LSB first
  for (i = 25; i > 0; i--) {
    if (output & 0x01) {
      digitalWrite(SPI_DATA_PIN, HIGH);  // output 1
    } else {
      digitalWrite(SPI_DATA_PIN, LOW);   // output 0
    }
    digitalWrite(SPI_CLOCK_PIN, HIGH);   // data latched by 5823 here
    digitalWrite(SPI_CLOCK_PIN, LOW);    // clock ends low
    output >>= 1;                        // shift output data
  }
  
  // terminate SPI transaction and set data low
  digitalWrite(SPI_ENABLE_PIN, HIGH);
  digitalWrite(SPI_DATA_PIN, LOW);
}

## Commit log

2015-04-26 initial commit of ZMR250 transmitter
    [5G8_fpv_tx.brd, 5G8_fpv_tx.sch]
2015-04-29 updated readme and added pictures of board
2015-04-29 added information about SPI modification to RX5823
2015-04-30 various updates to READMEs and images, added channel calculator spreadsheet
    [TX_Channel_Calculator.xlsx]
2015-05-01 updated attiny software fixing a number of problems
    [attiny84_transmitter.ino]
2015-05-01 added mounting information
2015-05-01 updated attiny firmware for more correct SPI operation and better defined button interface
    [TX_Channel_Calculator.xlsx]
2015-05-18 added BoM and updated README to reflect some minor issues
    [FPV_TX_BOM.xlsx]
2015-05-19 updated BOM error and added notes on interference testing results
    [FPV_TX_BOM.xlsx]
2015-06-19 added separate EAGLE directory and updated README and latest board files
    [5G8_fpv_tx.brd, 5G8_fpv_tx.sch]
2015-06-19 updated BOM
    [FPV_TX_BOM.xlsx]
2015-06-21 added picture of antenna

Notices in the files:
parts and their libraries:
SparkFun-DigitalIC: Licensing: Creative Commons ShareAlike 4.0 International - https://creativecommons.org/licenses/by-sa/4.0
